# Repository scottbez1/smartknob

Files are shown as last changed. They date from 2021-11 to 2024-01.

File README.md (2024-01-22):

# SmartKnob
SmartKnob is an open-source input device with software-configurable endstops and virtual detents.

A brushless gimbal motor is paired with a magnetic encoder to provide closed-loop torque feedback control, making it
possible to dynamically create and adjust the feel of detents and endstops.

Join the [Discord community](https://discord.gg/5jyhjcbTnR) to discuss the project with others, show off your build, or help answer each others' questions!




# Designs

## SmartKnob View
The "SmartKnob View" is the premium SmartKnob experience with an integrated display shown in my [demo video](https://www.youtube.com/watch?v=ip641WmY4pA). Under active development.

🎉 **Motors are [now available](https://www.sparkfun.com/products/20441)!** If you've been following this project,
you'll know that the recommended motors went out of stock nearly immediately after it was published.
Thanks to [the community](https://github.com/scottbez1/smartknob/issues/16#issuecomment-1094482805%5D), we were able to
identify the likely original manufacturer, and recently SparkFun Electronics has been getting them produced and regularly
[stocking them](https://www.sparkfun.com/products/20441)! (However, they've been selling out quickly each time they restock, so definitely sign up for backorder notifications if they're out of stock when you check). Thanks to everyone who helped search and investigate different
motor options along the way!

Features:
 - 240x240 round LCD ("GC9A01"), protected by 39.5mm watch glass on rotor
 - BLDC gimbal motor, with a hollow shaft for mechanically & electrically connecting the LCD
 - Powered by ESP32-PICO-V3-02 (Lilygo TMicro32 Plus module)
 - PCB flexure and SMD resistors used as strain gauges for press detection (haptic feedback provided via the motor)
 - 8 side-firing RGB LEDs (SK6812-SIDE-A) illuminate ring around the knob
 - USB-C (2.0) connector for 5V power and serial data/programming (CH340)
 - VEML7700 ambient light sensor for automatic backlight & LED intensity adjustment
 - Versatile back plate for mounting - use either 4x screws, or 2x 3M medium Command strips (with cutouts for accessing removal tabs after installation)
 - Front cover snaps on for easy access to the PCB

**Current status:** Not recommended for general use, but may be a fun project for an advanced electronics hobbyist.

### Demo video

<a href="https://www.youtube.com/watch?v=ip641WmY4pA">
    
</a>

### How it works
<a href="https://www.youtube.com/watch?v=Q76dMggUH1M">
    
</a>

### 3D CAD

Exploded view

Latest Fusion 360 Model: https://a360.co/3BzkU0n

#### DEMO: video editor timeline control

If you edit audio/video, imagine having a jog wheel where you could _feel_ the clip boundaries as you scrolled through the timeline. Then switch to playback speed control, with a wheel that's spring-loaded to return to "paused," with snaps at 1x, 2x, 4x, etc. The SmartKnob can do this; it just needs some software integrations to be written. Check out a demo using a SmartKnob prototype to control a mock video timeline:

<a href="https://www.youtube.com/watch?v=J9192DfZplk">
    
</a>

(you can actually try this demo yourself if you've already built a SmartKnob; plug it in over USB and go to https://scottbez1.github.io/smartknob/)

### Build your own?

While this is a "DIY" open-source project, it is not yet a mature plug-and-play project. If you intend to build your own, note that it requires advanced soldering experience to build - very small-pitch surface-mount soldering is required (reflow or hot air recommended), and assembly is quite time-consuming and delicate. Please go into it with the expectation that you will almost certainly need to be able to troubleshoot some hardware and firmware issues yourself - I recommend reviewing/understanding the schematics and basic firmware before jumping in!

More documentation on the BOM and what parts you need to order is coming in the future - thanks so much for your interest! Follow me on [Twitter](https://twitter.com/scottbez1) for the latest updates on this and other projects.

View the latest auto-generated (untested) [Base PCB Interactive BOM](https://smartknob-artifacts.s3.us-west-1.amazonaws.com/master/electronics/view_base-ibom.html) and [Screen PCB Interactive BOM](https://smartknob-artifacts.s3.us-west-1.amazonaws.com/master/electronics/view_screen-ibom.html) (or, the combined [BOM csv](https://smartknob-artifacts.s3.us-west-1.amazonaws.com/master/electronics/view_base-bom.csv)) for electronics/hardware parts list. ⚠️ These are auto-generated from the latest untested revision on GitHub. For tested/stable/recommended artifacts, use a [release](https://github.com/scottbez1/smartknob/releases) instead.

A few miscellaneous notes in the meantime:

 - There's limited space inside the LCD mount for wiring, and 8 wires need to fit through the hole in the center. I used 30 AWG wire-wrapping wire. Enamel-coated wire would probably work too.
 - Older versions of the design (as seen in the videos) used glued-on BF350-3AA strain gauges to detect presses; in v0.5 these were replaced with footprints for SMD resistors, which exhibit similar properties when stretched/compressed and are much easier to assemble. 
 - The TMC6300 is _tiny_ and has a bottom pad, so I would seriously consider getting a stencil along with the PCB order. Even with the stencil I needed to manually clean up some bridging afterward; I _highly_ recommend Chip Quik NC191 gel flux, available on [Amazon](https://amzn.to/3MGDSr5) (or use this [non-affiliate link](https://www.amazon.com/Smooth-Flow-No-Clean-syringe-plunger/dp/B08KJPG3NZ) instead) or from your electronics distributor of choice. Flux is also very helpful when soldering the LCD ribbon cable to to screen PCB.
 - For breadboard prototyping, the [TMC6300-BOB](https://www.trinamic.com/support/eval-kits/details/tmc6300-bob/) or SparkFun's [TMC6300 driver board](https://www.sparkfun.com/products/21867) are awesome and way easier to work with than the bare chip if you just want to play around with low current BLDC motors
 - For AliExpress purchases: I highly recommend **only** using AliExpress Standard Shipping (purchasing in the US). I have had multiple purchases take months or never get delivered when purchased with Cainiao or other low cost shipping options, whereas AliExpress Standard is very reliable and generally faster in my experience.
 - Make sure to check the [open issues](https://github.com/scottbez1/smartknob/issues) - this design is not yet "stable", so beware that everything may not go smoothly.

Future plans:
 - consider switch to using an ESP32-S3-MINI-1 module
 - get wifi configured and working (probably MQTT?). Currently memory is an issue with the full display framebuffer sprite. PSRAM might fix this (requires newer ESP-IDF & unreleased Arduino core, and from a brief test I got horrible performance with PSRAM enabled), or the next item might help reduce memory:
 - migrate to LVGL, for better display rendering and easy support for menus, etc. Shouldn't require a full 240x240x24b framebuffer in memory, freeing some for wifi, etc.
 - Home Assistant integration, or other real-world applications
 - ???
 - [Profit](https://github.com/sponsors/scottbez1/) 😉

#### Already built one?
Check out the [firmware/software documentation](https://paper.dropbox.com/doc/SmartKnob-firmware-and-software--B_oWj~L1dXqHgAqqYmhwwuqzAg-VUb9nq7btuhnHw5KlgJIH)
for tips on getting it programmed and hooking it up to your own software integrations.

If you've already uploaded the standard firmware and gone through the calibration process (see guide linked above if you don't know what this means),
go to https://scottbez1.github.io/smartknob/ to try out an interactive web-based demo that uses Web Serial to talk to a SmartKnob that's plugged into your
computer's USB port!

#### Base PCB

<a href="https://smartknob-artifacts.s3.us-west-1.amazonaws.com/master/electronics/view_base-front-3d.png">
    
</a>
<a href="https://smartknob-artifacts.s3.us-west-1.amazonaws.com/master/electronics/view_base-back-3d.png">
    
</a>

Ordering notes: use white soldermask, for reflecting light from RGB LED ring around the knob. Should be 1.2mm thick (not "standard" 1.6mm).

If you are ordering a stencil for solder paste from JLCPCB and plan to apply paste by hand (as
[shown in the video](https://youtu.be/Q76dMggUH1M?t=372)) without a stencil frame/machine, make sure to select
**"Customized size"** and enter smaller dimensions (e.g. 100mm x 100mm) to avoid getting a much larger stencil than you
need. This will also likely reduce the cost of shipping substantially! Also, select only the **Top** side; the bottom
only has 2 SMT components - the motor connector and VEML7700 ALS - so it's not worth getting a stencil for that.

Latest auto-generated (untested and likely broken!) artifacts⚠️:

[Schematic](https://smartknob-artifacts.s3.us-west-1.amazonaws.com/master/electronics/view_base-schematic.pdf)

[Interactive BOM](https://smartknob-artifacts.s3.us-west-1.amazonaws.com/master/electronics/view_base-ibom.html)

[PCB Packet](https://smartknob-artifacts.s3.us-west-1.amazonaws.com/master/electronics/view_base-pcb-packet.pdf)

[Gerbers](https://smartknob-artifacts.s3.us-west-1.amazonaws.com/master/electronics/view_base-jlc/gerbers.zip)

⚠️ For tested/stable/recommended artifacts, use a [release](https://github.com/scottbez1/smartknob/releases) instead.

#### Screen PCB

<a href="https://smartknob-artifacts.s3.us-west-1.amazonaws.com/master/electronics/view_screen-front-3d.png">
    
</a>
<a href="https://smartknob-artifacts.s3.us-west-1.amazonaws.com/master/electronics/view_screen-back-3d.png">
    
</a>

Ordering notes: Must be 1.2mm thick (not "standard" 1.6mm) per mechanical design. (The PCB silkscreen mentions 0.6mm thickness - this is the thickness of the **VHB tape** for adhering the LCD; the PCB should be 1.2mm thick)

There are few enough components on the Screen PCB that I chose to hand-solder them rather than reflow with solder paste
and a stencil, but if you order a stencil, see the note above about selecting a "Customized size" to be easier to
handle and save on shipping. Also make sure to select the **Bottom** side only; all the components are on the bottom
side of the screen PCB.

Latest auto-generated (untested and likely broken!) artifacts⚠️:

[Schematic](https://smartknob-artifacts.s3.us-west-1.amazonaws.com/master/electronics/view_screen-schematic.pdf)

[Interactive BOM](https://smartknob-artifacts.s3.us-west-1.amazonaws.com/master/electronics/view_screen-ibom.html)

[PCB Packet](https://smartknob-artifacts.s3.us-west-1.amazonaws.com/master/electronics/view_screen-pcb-packet.pdf)

[Gerbers](https://smartknob-artifacts.s3.us-west-1.amazonaws.com/master/electronics/view_screen-jlc/gerbers.zip)

⚠️ For tested/stable/recommended artifacts, use a [release](https://github.com/scottbez1/smartknob/releases) instead.

#### Printed parts
You will need six printed parts. The current stable designs can be found as STL assets in the [v185 mechanical release](https://github.com/scottbez1/smartknob/releases/tag/releases%2Fmechanical%2Fv185-dummy-tag) or you can export the latest untested designs from the CAD model by opening it in Fusion 360: https://a360.co/3BzkU0n

The parts can _probably_ be FDM 3D printed with a well-tuned printer, but the parts shown in videos/photos were MJF printed in nylon for tight tolerances and better surface finish. 

If you wanted a simpler build, you could omit the LCD and just merge the knob + glass from the model into a single STL to get a closed-top knob.

Export and print the following 6 parts:
* `Enclosure`
* `Knob` (RotorAssembly->KnobAssembly->Knob)
* `ScreenPlatform`
* `RotorSpacer` (RotorAssembly->RotorSpacer)
* `MountBase`
* `BackPlate`

⚠️ If you opt to go for MJF Nylon printing from JLCPCB, their system may complain about `< 0.8mm wall thickness detected` on the `MountBase`, `ScreenPlatform` and `RotorSpacer` parts. This appears to be a false positive, possibly on some of the print tapers. You should be able to ignore this, as all print orders at JLCPCB are subject to a final manual review, and they will contact you by email if there are any job-stopping issues or risks with your prints.

## NanoFOC (3rd party)
If you're looking to tinker with FOC/haptic feedback, but don't want to build a full SmartKnob View yourself, I can
recommend the NanoFOC DevKit++, an [open-source design](https://github.com/katbinaris/nanofoc_devkit) made and
[sold](https://store.binaris.io/products/nanofoc-devkit) by a member of the SmartKnob community! It's super compact
and is a great testbed or core for building your own BLDC-based haptic input device.

Image of the NanoFOC PCB

The NanoFOC uses an ESP32-S3, and the SmartKnob firmware works on it out of the box; just select the `nanofoc`
environment in PlatformIO rather than the `view` environment when uploading.

# Frequently Asked Questions (FAQ)

### Can I use this cheap gimbal BLDC motor I found on AliExpress?

I can't stop you, but I will caution that **you probably won't be super happy with it** depending on your intended application.

Nearly every off-the-shelf BLDC gimbal motor that the community has tested (which is pretty much ALL the cheap ones you'll find on AliExpress, trust me) has
_moderate to severge cogging_. That means the motor wants to snap to certain positions by itself even when unpowered. This means you won't be able to get
completely smooth rotation when virtual detents are turned off, and the motor's cogging may interfere with or overpower the virtual detents, particularly if
you set them to lower strength or make then very fine-grained.

The recommended motor is definitely the best (i.e. lowest cogging) off-the-shelf motor we've come across so far, and is the only readily-available motor
that I would consider "good" for this application.

If you've found another motor that is completely smooth when unpowered, we'd LOVE to hear about it in the discord; if you're wondering about some cheap motor
you saw online, either just order one and try it for yourself, or ask about it in discord but don't be surprised (or offended) if the response you get is
something terse like "nope, no good".

### How much does it cost?

I wish I could tell you now, but I don't actually know off the top of my head. Check back soon - I've only built a few so far, which was the result of a bunch of tinkering and prototyping over an extended period, so I don't have all the expenses tallied up yet. Probably less than $200 in parts? But some items have gotten more expensive, and you may be limited by minimum order quantities or shipping charges from multiple separate suppliers.

### Does it work with XYZ?

Not yet, regardless of whatever "XYZ" you're thinking of. So far I've only implemented enough firmware for the demo shown in the video, so you can't actually use it for anything productive yet. The basic detent configuration API is there, but not much else. Lots of firmware work remains to be done. If you build one, I'd love your help adding support for "XYZ" though!

### Can I buy one as a kit or already assembled?

Probably not? Or at least, I don't have any immediate plans to sell them myself. It's not that I don't want you to be happy, but hardware is a hard business and I just work on this stuff in my free time.

It's open source with a fairly permissive license though, so in theory anyone could start offering kits/assemblies. If someone does go down that route of selling them, note that attribution is
 _required_ (and I wouldn't say no to [royalties/tips/thanks](https://github.com/sponsors/scottbez1/) if you're in a giving mood 🙂).

# Firmware and Software
More extensive documentation of the firmware and software (and how to get started) can be found in the dedicated [SmartKnob Firmware and Software Guide](https://paper.dropbox.com/doc/SmartKnob-firmware-and-software--Byho6npe9XvZLZLxJ_8bK5TqAg-VUb9nq7btuhnHw5KlgJIH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)

## General Component Info

### Magnetic encoders

#### MT6701 (MagnTek)
Excellent sensor at a reasonable price - highly recommended. Less noisy than TLV493D, and more responsive (control loop is more stable) using SSI.

 - Lots of IO options - SSI, I2C, and ABZ - should offer good response latency
 - SSI includes CRC to validate data
 - No power-down or low-power options - may not be ideal for battery-powered devices
 - Not available from US distributors (Mouser, Digi-Key)

[Datasheet](http://www.magntek.com.cn/upload/MT6701_Rev.1.5.pdf)

[Ordering (LCSC)](https://lcsc.com/product-detail/Angle-Linear-Position-Sensors_Magn-Tek-MT6701CT-STD_C2856764.html)

#### TLV493D (Infineon)
Not used in the SmartKnob view, but a common/popular magnetic encoder in general. It's a mediocre choice for a haptic feedback implementation. Easy to prototype with using [Adafruit's QWIIC breakout board](https://www.adafruit.com/product/4366).

In my testing, it's noisy, requiring filtering/smoothing that can slow responsiveness, hurting control loop stability. Or, with less filtering, the noise
can easily be "amplified" by the derivative component in the PID motor torque controller, causing audible (and tactile) humming/buzzing.

But the bigger issue is that there is apparently a known silicon issue that causes the internal ADC to sometimes completely lock up, requiring a full reset and re-configuration, which can cause delays/gaps in data! See section
5.6 in the [User Manual](https://www.infineon.com/dgdl/Infineon-TLV493D-A1B6_3DMagnetic-UM-v01_03-EN.pdf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)

    In the Master Controlled Mode (MCM) or the Fast Mode (FM) the ADC conversion may hang up. A hang up can
    be detected by:
     - Frame Counter (FRM) counter stucks and does not increment anymore.

In my experience testing 4 different Adafruit breakout boards, 2 of them (50%) regularly exhibit this lockup behavior within a minute or two of use. It is possible to detect and auto-reset (and there is code in the project to do so), but it is slow and may cause undesirable jumps/delays if the sensor locks up often.

[Datasheet](https://www.mouser.com/datasheet/2/196/Infineon_TLV493D_A1B6_DataSheet_v01_10_EN-1227967.pdf)

#### AS5600 (AMS)
A mediocre choice. Cheap breakout boards are readily available.

In my testing, it's fairly noisy (anecdotally, noisier than the TLV493d), requiring filtering/smoothing that can slow responsiveness, hurting control loop stability. Additionally, it saturates at a lower magnetic field strength than other sensors I tested, requiring a significant air gap (8-10mm) when used with a strong neodymium diametric magnet like [Radial Magnets 8995](https://www.digikey.com/en/products/detail/radial-magnets-inc/8995/5126077).

[Datasheet](https://ams.com/documents/20143/36005/AS5600_DS000365_5-00.pdf)

### Motor drivers
#### TMC6300-LA
This is a relatively new IC and it's a perfect match! There generally aren't any other drivers (with integrated fets) that meet the requirements for the low-voltage and low-current motors used in this project (DRV8316 might work, but has not been tested).

Highlights:
 - 2-11V DC motor supply input
 - Up to 1.2A RMS
 - Tiny (3x3mm QFN)

 [Datasheet](https://www.trinamic.com/fileadmin/assets/Products/ICs_Documents/TMC6300_datasheet_rev1.07.pdf)

 [Product page](https://www.trinamic.com/products/integrated-circuits/details/tmc6300-la/)

### Motors
#### 32mm Rotor, Hollow Shaft, Diametric magnet
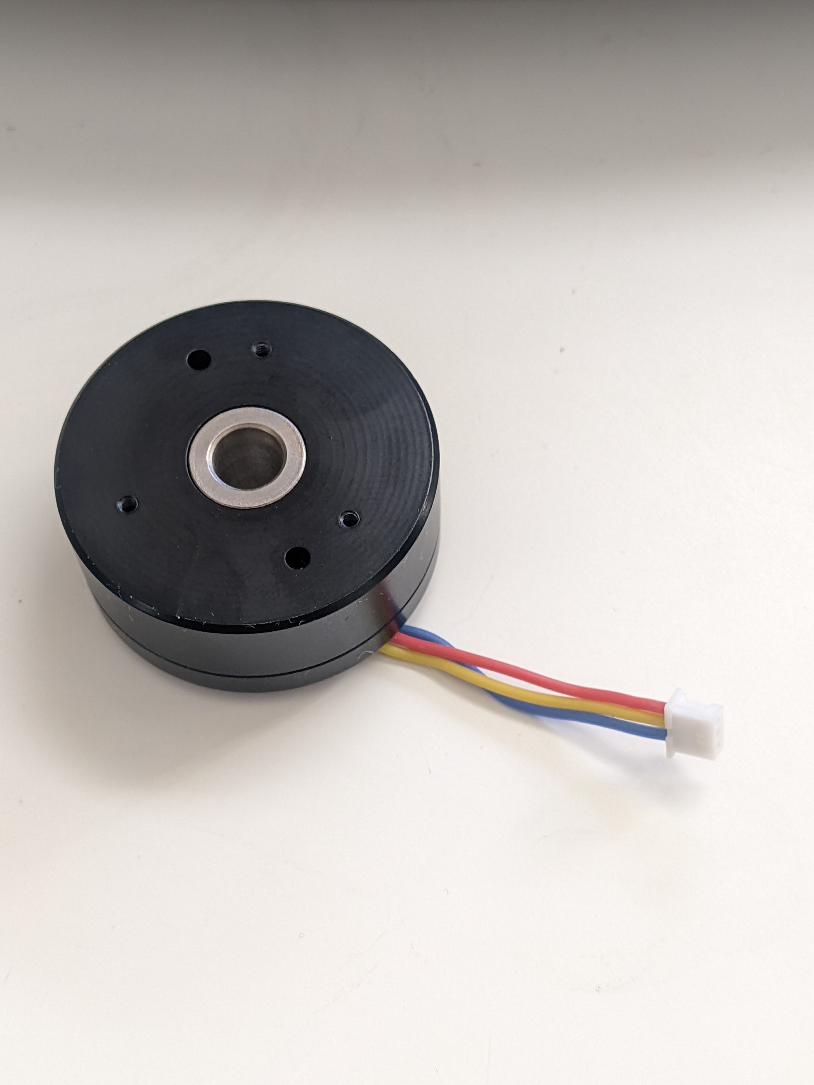
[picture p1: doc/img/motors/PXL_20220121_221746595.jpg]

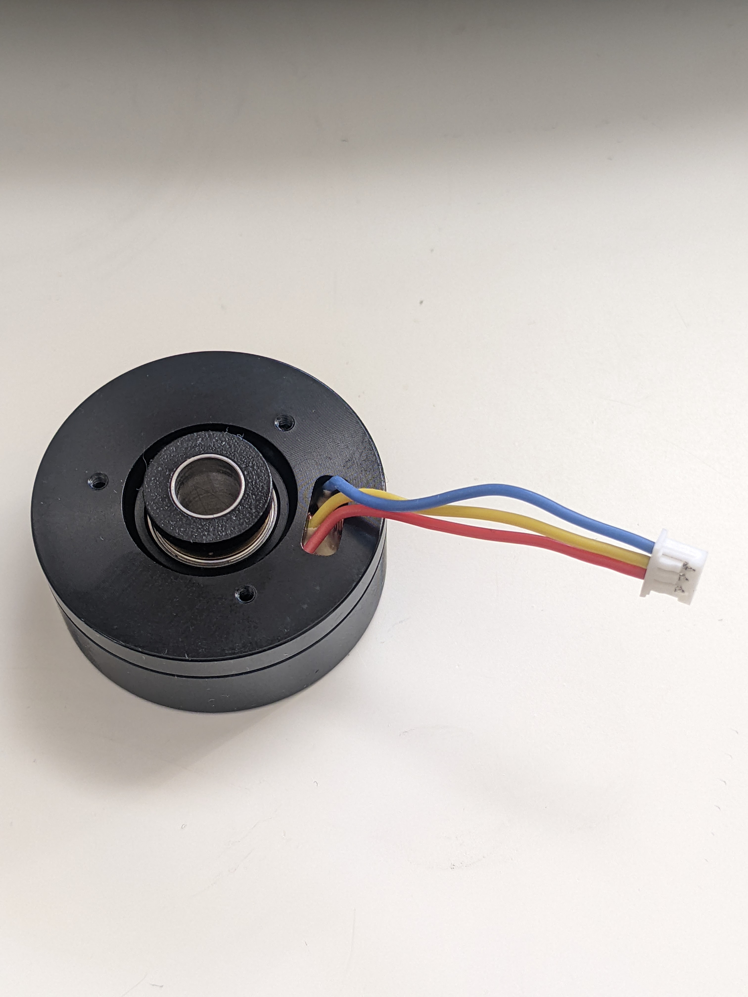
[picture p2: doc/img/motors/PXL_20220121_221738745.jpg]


- 32mm rotor
- 15mm overall height (including magnet), 12.75mm height w/o magnet, 9mm rotor height
- low/zero cogging - excellent for completely smooth input
- 5.9mm hollow shaft
- built-in diametric magnet for encoder
- Proven option

This is overall the easiest motor to get started with. Low cogging and a built-in diametric magnet are great!

Available [from SparkFun](https://www.sparkfun.com/products/20441)!

# Acknowledgements
This project was greatly inspired by Jesse Schoch's video "[haptic textures and virtual detents](https://www.youtube.com/watch?v=1gPQfDkX3BU)" and the
corresponding [discussion in the SimpleFOC community](https://community.simplefoc.com/t/haptic-textures/301). Seriously, this project wouldn't exist if not for that video - thank you Jesse!

# License

This project is licensed under Apache v2 (software, electronics, documentation) and Creative Commons Attribution 4.0 (hardware/mechanical) (see [LICENSE.txt](LICENSE.txt) and [Creative Commons](https://creativecommons.org/licenses/by/4.0/)).

    Copyright 2022 Scott Bezek
    
    Licensed under the Apache License, Version 2.0 (the "License");
    you may not use this file except in compliance with the License.
    You may obtain a copy of the License at
    
        http://www.apache.org/licenses/LICENSE-2.0
    
    Unless required by applicable law or agreed to in writing, software
    distributed under the License is distributed on an "AS IS" BASIS,
    WITHOUT WARRANTIES OR CONDITIONS OF ANY KIND, either express or implied.
    See the License for the specific language governing permissions and
    limitations under the License.

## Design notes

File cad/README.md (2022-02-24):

# CAD

Most CAD work is done in Fusion 360 and versioned outside of this git repo.

# Assemblies
## SmartKnob View
 - [Complete SmartKnob View assembly](https://a360.co/3BzkU0n)

## Handheld
 - [Case bottom](https://a360.co/3LM82se) For breadboard with power rails removed.
 - [Motor adapter](https://a360.co/3LO03eC) Connects motor to Adafruit TLV493d adapter board, and screws into Case
 - [Thumbwheel](https://a360.co/3H3jSee) Test thumbwheel for motor rotor, for turning from the side

# Motors
Note that all measurements were done by hand and will be approximate. Chamfers & fillets are approximated.

## 32mm
 - [Motor model](https://a360.co/3H8LUFi)

## 17mm
 - [Motor model](https://a360.co/3sYa93Y)
 - [Spacer](https://a360.co/3H3xh5M) (screw at the bottom is replaced with a longer M1.4 screw with this spacer inserted; diametric magnet is glued to screw)
 - [Dummy test jig](https://a360.co/3sPQgvB)

 ## 15mm
 - [Motor model](https://a360.co/34N1nOa)
 - [Magnet spacer](https://a360.co/3532Tvb)
 - [Magnet gluing jig](https://a360.co/3I1xbx6)
 - [Adapter](https://a360.co/35gC86B) - mount motor to Adafruit TLV493d adapter board

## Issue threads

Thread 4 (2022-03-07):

Increase vertical clearance between LCD and knob

scottbez1, 2022-03-07:
Could use another ~0.5mm between LCD and the inside/inner-bottom face of the knob, to account for assembly imperfections, to ensure the knob doesn't scrape on the screen.

It should be ok to decrease the vertical clearance below the screen pcb correspondingly; there's more clearance here than necessary.

scottbez1, 2022-03-14:
Increased by 0.5mm in v175 & v181

Closed 2022-03-14.

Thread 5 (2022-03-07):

Consider increasing diameter of screen PCB

scottbez1, 2022-03-07:
To avoid LED light leakage around the LCD, it might make sense to increase the PCB's diameter. Might also be helpful to add silkscreen alignment marks on the top side to help with centering the LCD.

Need to make sure it's still narrow enough for the knob/rotor to slide past it during assembly.

scottbez1, 2022-03-14:
Decided to add a light baffle to the MountBase instead, in v179. The light baffle is right above the LEDs so should be more effective at blocking light (any remaining light leakage will have a higher incident angle with ID wall of the knob compared to using the screen PCB as a baffle). It will require supports for FDM printing, but this shouldn't be a big deal since this is non-cosmetic and tolerances are not an issue on the underside of the light baffle (plenty of space between the baffle and LED for vestigial support blemishes)

Keeping screen pcb diameter <= lcd diameter is preferable to avoid having exposed VHB when viewed from the top (or else you'd need to trim the VHB inset from the PCB edge...)

Closed 2022-03-14.

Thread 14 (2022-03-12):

Idea: ethernet/PoE

nagyrobi, 2022-03-12:
Is there any plan to have a version supporting wired Ethernet connetion?

ESP32 can accomodate with various Ethernet PHY chips, also combined with an 802.3af PoE supply this project could really kick ass in the home automation world. Think of this also as mounted on wall on the end of a CAT5 cable supplying both data and power...

scottbez1, 2022-03-13:
No plans for Ethernet. It would definitely be cool, but probably not something I will personally prioritize at the moment. My main priorities are:
- better documentation
- firmware improvements (graphics, configuration api, serial protocol, getting wifi working)

But the other issue that comes up is limited IO - with the current ESP32 module I'm using, all outputs are currently in use (except IO0 I guess) and the only open pins are inputs (34, 35, and 39).

The LCD (6 GPIO) and motor driver (7 GPIO) are both IO heavy, and then there's I2C, magnetic sensor, and strain gauge amplifier, so it would require a pretty substantial change to be able to free up pins to support an ethernet PHY.

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

There's probably a hybrid approach where you use an external ethernet<->serial adapter and connect this in place of the CH340 USB serial interface, but I'm not familiar with what's available in that space, or how to integrate it. In that case it would be helpful to expose RX and TX as testpoints for easier connection.

nagyrobi, 2022-03-14:
I suggest for develompent on the longer term... maybe you could use a GPIO expander like MCP23017 for more basic stuff...

Ethernet-Serial conversion limits functionality a lot, as there's an extra middleware needed to convert serial-like protocol to whatever is needed. Ethernet connection should be equivalent to wifi in terms of functionality.

scottbez1, 2022-03-15:
Added RX/TX testpoints, so hardwired serial communication without a USB connection is easier to hook up if desired.

However, the remainder of the discussion in this issue regarding first-class ethernet support is outside the scope of planned features, so in the interest of keeping the issues list clean, closing this as wontfix.

scottbez1, 2022-04-07:
Per #51, I'm reopening this issue as a general place for brainstorming/discussion around ethernet and PoE. Like I mentioned in that issue, I want to keep this project extremely focused for now, so I don't see ethernet support realistically being added any time soon, but doesn't hurt to have a place (this thread) for discussion in the meantime

austinscreations, 2022-04-13:
for POE i've been using https://www.aliexpress.com/item/1005002768318128.html
(keyword: SDAPO DP1435 - should link die)

combined with the w5500 spi ethernet IC - which requires 5 pins. sck, miso, mosi, cs, and a reset pin (not mcu reset - needs to be controllable IO)

Timvrakas, 2022-09-15:
I'm not sure Ethernet is needed for this simple of a device, PoE adds a significant cost and complexity electrically. If you were integrating this into an industrial/home automation system I can see the appeal, but if I were running more than one or two units I think I would quickly prefer RS485 or CAN or BASE-T1L or similar to link them to a controller that in turn had Ethernet.

If you're looking for a PoE module, I will recommend https://silvertel.com/ they make high quality PoE modules.

sanderkooger, 2023-10-19:
Another option would maybe be skip the POE and Ethernet connectivity, Mount the smart knob on a (in wall) switch box and use the power thats already there? Then use WIFI for communication.

Is this a viable option too?

sanderkooger, 2023-10-19:
@scottbez1 Congrats on this project BTW, This could be the start of something really cool.

At the moment, I'm researching lights control for my home. If Wi-Fi becomes available and i could have the knob send out API requests over Wi-Fi. I should be golden. I'm also looking into thermostats that i can talk too over an API.

Have you ever thought of promoting your project on the Wled https://github.com/Aircoookie/WLED

I think you would find a lot more enthusiasts there who have and electronic knowledge and could maybe contribute.

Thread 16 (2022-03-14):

Motor out of stock

mattkerrison, 2022-03-14:
Not a major issue as you've said you've got several others on the way for testing, but the link to the motor you used is now out of stock:

[AliExpress](https://www.aliexpress.com/item/1005001384349991.html)

scottbez1, 2022-03-14:
Yeah, I'm hoping this is just a temporary out of stock issue, but the seller actually has another listing that looks essentially identical (though a tiny bit more expensive) and is still in stock (for now) - https://www.aliexpress.com/item/4001356858801.html

I've ordered a handful of those myself and will confirm whether they're the same in ~2 weeks when they arrive :stuck_out_tongue: Probably worth snagging a few now regardless since they're pretty cheap.

My fear is that they may just be selling off "new old stock" from some short-lived product and the motors are not actively being manufactured any longer, in which case the interest in this project could quickly consume what's available. :crossed_fingers: Hopefully that's not the case though, as there are basically zero other cheap options for hollow shaft BLDC motors with low KV and zero cogging torque that I could find...

SpuriousGer, 2022-03-25:
Your update on March 24th seems quite discouraging, does this mean the project is dead? Seems like one of the coolest ones I've seen in ages.

C44Supra, 2022-03-25:
It gets worse, the other listing that @scottbez1 linked to is gone now too. I had an order for a couple of those and that order was simply cancelled earlier this morning, so that double listing seems to have been an oversight. The motors from that seller (and two other sellers as well) that looked similar by had wires running through the hollow shaft already, those have also been removed. Well not removed, I created two orders from separate sellers last night and both of those items have been changed into a completely different item. I haven't been able to find a replacement motor yet.

I'm not sure what other motors @scottbez1 has bought to test, but I would love to know. It would be very helpful to know which motors we should avoid specifically.

scottbez1, 2022-03-25:
Responding from my phone, so pardon the brevity.

I don't want to call the project dead quite so soon, but it's certainly not
looking very good at all...

Regarding other motors, I basically ordered every single small BLDC from
that AliExpress seller (which is most of the cheap motors I could find on
AliExpress in general) and there's not good news there, unfortunately. All
of the other hollow-shaft motors had noticeable or substantial cogging,
making them poor candidates.

I'll follow up with more details when I have some time this weekend,
including a list of all the motors I've personally checked.

C44Supra, 2022-03-25:
I certainly wouldn't call it dead in the water, just needs some adjustments for a more widely available motor. I'm tempted to grab a more common 2804 or maybe 2204. Lots of varieties though and not a whole lot that either have an axial magnet or room for one.

SpuriousGer, 2022-03-25:
> Responding from my phone, so pardon the brevity. I don't want to call the project dead quite so soon, but it's certainly not looking very good at all... Regarding other motors, I basically ordered every single small BLDC from that AliExpress seller (which is most of the cheap motors I could find on AliExpress in general) and there's not good news there, unfortunately. All of the other hollow-shaft motors had noticeable or substantial cogging, making them poor candidates. I'll follow up with more details when I have some time this weekend, including a list of all the motors I've personally checked.

You mention cheap, is it a prerequisite that it is really cheap or are there other motors that might fit the bill but are more expensive?

C44Supra, 2022-03-25:
@scottbez1 would be helpful to know what sort of BLDC motor you're using at the moment. From what I understand the majority of cogging is a result of the type and size of magnets used in the rotating part. In an effort to generate as much torque as possible, most manufacturers opt for neodymium magnets which are significantly more powerful compared to ferrite magnets.

jimius, 2022-03-26:
I don't know a lot about motors, but I did find this:
https://store.cubemars.com/ from a company called Tmotors (
https://uav-en.tmotor.com/).
Again, no idea if the specs match anything you need.

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

dsamarin1, 2022-03-26:
Seconding what @C44Supra said, perhaps logging here the specs of your currently best-performing motor so the group can help hunt down a replacement, especially once the AliExpress pages disappear. I'm thinking these are important: Critical dimensions, Kv, electrical specs (ex. maybe max torque can indicate something else useful), keywords. Others?

In the future, the move is probably a redesign for the more common outrunner motors on hobby RC websites. Considering tackling part of this myself.

LeonBentrup, 2022-03-27:
It looks like [newegg](https://www.newegg.com/p/298-00HJ-001V2) has the motor but only with a slipring installed. removing that wouldnt be a problem, but the 50$ pricetag is. i think the best way going forward would be using a standard gimbal motor and putting on a diametrical ringmagnet from [mcmastercarr](https://www.mcmaster.com/ring-magnets/direction-of-magnetization~through-diameter/) or so. something like those 2804, 2805or 3413 look more common and could propably be used

C44Supra, 2022-03-27:
@LeonBentrup that listing on Newegg is from a chinese reseller as well. It was listed by at least 3 different vendors on AliExpress but all three have removed the exact same listings at the same time. I'd say there's good chance it's one and the same vendor, just active under a couple of different names. That said, I did get a reply from the AliExpress seller earlier today:

> Sorry to tell you that we can't send this item out. A local buyer picked all this item a few days ago and our workmate forget to remind us to end this listing.
We contacted several suppliers and they don't have this item in stock. And also can't give sure reply when the item will be available.
But we have the other similar item in our shop,could you please check it meet your need or not?

The other item they are referring to is https://www.aliexpress.com/item/1005003751799249.html It looks somewhat similar but is missing the diametrical magnet. There's also not enough shaft protruding to stick a magnet onto so that would be a no good either.

It's also quite problematic that their motor numbers seem to reference the outer diameter and height of the entire motor, where as other suppliers generally reference the internal dimensions of the actual motor parts. The 3413 for instance is pretty much the same as a 2804.

I did "some" looking around on AliBaba last night / this morning ( / what day is it again?), and found a supplier that has a motor that shows potential. They're not too expensive, have a 7mm diameter protruding shaft on the bottom and looks to be good design. I've contacted them and are waiting for a reply with more data about that specific motor.

A quick search on Amazon led me to some 10x3x7 (outer diameter x thickness x inner diameter) diametric magnets. I think thinner ones would work, too, though.

LeonBentrup, 2022-03-27:
@C44Supra Does it have to to be a motor with a stick out shaft? for example the mks servo42 just uses superglue and two of those are running fine on my 3d printer. its not a hollow shaft there but those [cheap 2804](https://de.aliexpress.com/item/1005001968864724.html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,scm-url:1007.40000.267768.0,pvid:cdc11d7c-d8bd-49ea-8f4c-22b666c9050f,tpp_buckets:668%232846%238112%23502&pdp_ext_f=%257B%2522sku_id%2522%253A%252212000018267338478%2522%252C%2522sceneId%2522%253A%252230050%2522%257D&pdp_pi=-1%253B3.03%253B-1%253B-1%2540salePrice%253BEUR%253Brecommend-recommend) look like you could glue it on there directly. Sticking a 6mm rod with some paper(to not glue the rod in there) down the hollow shaft you could even get it centered pretty good. and since its not turning with 2000 rpm i wouldnt be afraid of the glue giving up
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
jtsfour, 2022-04-01:
@C44Supra

Thanks for the input.  I was just now doing some digging into the magnets.  What if we standardized around a motor design even with neodymium magnets (Like the 2804).  Couldn't we just remove the Neodymium magnets from the rotor and replace it with a Ferrite Ring of our own specifications?  How are these magnets installed?  Could we use a heat gun and pull them?

I found this magnet supplier that does custom multipolar ferrite rings.  Maybe this could be an easier option over finding motors that have been specifically built weaker and cheaper.  We could use a small crowdsource and buy a couple thousand and use them collectively.

https://www.hsmagnets.com/product/customized-radial-multipole-ferrite-rotor-magnets/

I am not an engineer.  Maybe someone with more experience could weigh in on this thought?

C44Supra, 2022-04-01:
@jtsfour

That would certainly be an option. I don't have any motors on hand just yet, but I suspect the magnets are being glued in, likely with a two part epoxy of sorts. The likelyhood of removing the magnets without destroying them or the rotor itself are likely slim to none.

That said, you may be on to something. I'll ask the manufacturers if they'd be willing to sell motors without magnets in the rotor at all.

Multipolar ring magnets can be found in all shapes and sizes on Alibaba as well. Finding one that fits the bill might be a bit of a challenge though.

mcmadhatter, 2022-04-01:
I have a "Power Motor GBM2804R 2804 Gimbal Motor with Aluminum case /Slipring /AS5048A Magnetic Encoder for camera stabilizer" on order for something else, but I'll try it out and see what it is like beforehand.

scottbez1, 2022-04-01:
Just for the heck of it, I submitted an Alibaba RFQ with the details and photos of the existing motors (32mm rotor, 6mm ID, 14P12N, etc), just in case the original manufacturer is still around and can easily spin up production of it again, or in case another manufacturer is able to produce an identical product. Certainly would be nice if it can be found and avoid the need to redesign the mechanics. Probably unlikely, but figured it's worth a shot.

scottbez1, 2022-04-02:
I've ordered some samples of the 2608 with ring magnet (from "Flash Hobby" Huizhou Feishun Technology), asking for a couple 5 ohm and a couple with 8 ohm windings to see how they compare.

Apparently there weren't readily available ferrite ring magnets for the 2606 size, so they will not make samples of that size for now.

Samples will ship via DHL Express, so depending on how long manufacturing takes I would hope to have them within a few weeks to evaluate them.

A big thank you to all the GitHub [sponsors](https://github.com/sponsors/scottbez1/) for helping fund experimentation like this! :heart:

If you're interested in eventually purchasing a motor (still a long way away and motor still TBD) - can you fill out [this quick anonymous survey](https://forms.gle/PtuVDrpcA2niVDCL9) so I can get a sense of total interest quantity, geographical distribution, and pricing? To somewhat set expectations, based on what I'm seeing I would guess that it will cost somewhere between US$25-50 per motor unless we can find something suitable that's already being widely manufactured and distributed, unfortunately...

 And of course let me know if you find other interesting motors or suppliers and I am happy to place more sample orders!

scottbez1, 2022-04-02:
@jtsfour thanks for
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

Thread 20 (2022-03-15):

Screen PCB thickness

Zomhad, 2022-03-15:
First of all thanks for open-sourcing this awesome design! I just noticed that the readme states the screen PCB must be 1.2mm thick ("Ordering notes: Must be 1.2mm thick (not "standard" 1.6mm) per mechanical design.") but on the silkscreen of the PCB there's a big "0.6mm thick" label. Probably just a small copy and paste mistake from the ordering notes of the base PCB, thought I'd mention it anyway.

PS: Can't wait for my PCB and parts to arrive and build one up. :-)

scottbez1, 2022-03-15:
Thanks for bringing this up!

Both are actually correct, if you can believe it. 1.2mm thickness PCB is correct, and the 0.6mm thick label on the silkscreen is meant to go with the "VHB 5925" text to clarify that the expectation is for 0.6mm VHB tape as opposed to the more common VHB 5952 (isn't that confusing product numbering?!) which is 1.1mm thick.

Let me think about how to make this more clear though, as I can totally understand the mixup.

I've been thinking about adding virtual footprints to the screen PCB for the double-sided tape, in which case the silkscreen clarification is probably not needed anymore since I can put a part number and clarifying comment for the VHB items which will appear in the auto-generated BOM directly.

scottbez1, 2022-03-15:
(another possible option I'm considering is just switching to 1.1mm VHB 5952 since it's more commonly found anyway, and just add another .5mm of vertical clearance inside the knob to accommodate)

Closed 2022-03-28.

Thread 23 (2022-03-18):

Pick & Place File

tallAldi, 2022-03-18:
Would it be possible to include a simple pick & place file in addition to the bom?
I'm not that experienced with smd soldering and would like to order the pcbs already assembled at factory, at least for the general stuff like resistors and capacitors.

scottbez1, 2022-03-18:
Are you thinking JLCPCB or another manufacturer? In theory this shouldn't be too difficult to support since I'm already using KiKit to export the gerbers (I may have to swap some LCSC part numbers for ones in JLC's PCBA part library), but one potential concern is that the finest pitch/most difficult part, the TMC6300, is not in JLC's part library for assembly so you'd still need to solder it yourself. At that point I'm not sure how much it helps to have the resistors and capacitors pre-assembled...

Here's a photo for reference - the small capacitors here are 0603 and the bigger capacitor is 0805:
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

tallAldi, 2022-03-25:
Yes exactly I was thinking JLCPCB. I think I can adjust the part numbers myself, the important thing to have is the coordinates in the picker files.
If I want to use a different manufacturer I have to adjust the part numbers anyways.
Good point regarding the TMC6300 though, maybe I have to solder that one myself, but then at least I don't have to worry about the rest.

KartoffelToby, 2022-03-30:
maybe pcbway is an option with a https://www.pcbway.com/project/sponsor/ sounds good, looks like its possible to make a "include all" package here with 3D Print and PCB assembled

tallAldi, 2022-04-08:
thanks for the BOM and CPL but I think there is something wrong with your export scripts as the CSVs are not formatted correctly:
`<Error>
<Code>AccessDenied</Code>
<Message>Access Denied</Message>
<RequestId>04005S033CFPDBGC</RequestId>
<HostId>
hrsQX0Zd4Dm7yARZxQnLXX2OTdabTdvb/b2LqfneL4g2Y6e8PpY6g72ds2pVmiQwefNG6p+Uq7I=
</HostId>
</Error>`

D-Buckingham, 2022-06-14:
Dear Scottbez1,
I really enjoy your design and the implementation you did is simply awesome.
I am at the same point as tallAldi and I would really appreciate it, if you could add centroid files in the releases. I tried to extract it myself with altrium from the gerbers, but somewhere I am stuck between errors or incomplete lists...
Thanks a lot!!!
PS: I get the same error message as tallAldi.
PPS: My chosen manufacturer is PCBWay ;)

SpuriousGer, 2022-10-07:
So, I contacted PCBWay and they said they'd be able to support this. What I don't really understand is: what do I need beyond it. I need to upload something here: https://www.pcbway.com/quotesmt.aspx
But what do I fill out and which files do I need to upload?

kquinsland, 2022-10-08:
> What I don't really understand is: what do I need beyond it. I need to upload something here: https://www.pcbway.com/quotesmt.aspx
> But what do I fill out and which files do I need to upload?

They're looking for several files but at a high level, the data they need fits into one of three big groups:

- the grbl files; one for each layer of the PCB. All/Most of these layers should share a common origin or fiducial point and some layers may contain notes about a particular feature or intention. This is typically sent as a ZIP file and it's the bare minimum you need to get a PCB made.
- the list of part numbers. If you're not going to use pcbway parts, there's some additional glue around which parts you supply and which they do. I don't know what this glue looks like, but i'd bet $ that it involves some back/forth with their support staff.
- a file that indicates the X/Y location (relative to the common fiducial / origin) for each of the part number(s).

The third group is commonly called the "pick and place" file... which is being discussed here :D.

The exact format for each will depend on the place doing the work; they all have their own rules around what they can/can't do ... etc.

Google will help you locate the rules / supported features for a board shop and then the rest is figuring out how to get the design software to spit out the files in the format(s) that the board house will accept.

**right now** one of the bigger questions is around _where_ to get the boards made. Not every board shop has the right part(s) in stock. Ideally, there would be a single part supplier that has a close relationship with the board shop so we only needed one set of part numbers.

SpuriousGer, 2022-10-08:
> **right now** one of the bigger questions is around _where_ to get the boards made. Not every board shop has the right part(s) in stock. Ideally, there would be a single part supplier that has a close relationship with the board shop so we only needed one set of part numbers.

Thanks a lot for the thorough reply, very helpful!
I think we have a list of those pick and place files, don't we:
https://smartknob-artifacts.s3.us-west-1.amazonaws.com/master/electronics/view_base-ibom.html
https://smartknob-artifacts.s3.us-west-1.amazonaws.com/master/electronics/view_screen-ibom.html

Or is this again something else?

I am trying to work with PCBWay on how to get this done. But I am so limited in my skills, I basically have two things: money (so I am happy to pay anyone for their time to assemble those lists) and the willingness to engage with them to have prototypes build and take the risk.

kquinsland, 2022-10-08:
> Or is this again something else?

That's a "human friendly" version of the data.  Look at the `LCSC` column on either and compare with the `Mouser` and `Digikey`. No one supplier has a part number for everything that's required which is the biggest blocker at the moment.

> I am trying to work with PCBWay on how to get this done.

See if you can find out what quantity they need for external parts.  I would imagine that it's probably a reasonably big number but if not, then you might be able to coordinate a small group buy.  E.G.: if they're willing to do a production run of only 10 boards using (some) customer supplied / 3rd party parts then you only need to find 10 boards worth of parts from which ever supplier has the parts that PCBWay does not have and ship them to PCBWay.

SpuriousGer, 2022-10-13:
I have received feedback from PCBWay. Attached is the Excel. I would require some help on this. Who could help? I think it looks promising overall.
[T-B2W570125A-5sets-view_base-bom(2022-10-13).xls](https://github.com/scottbez1/smartknob/files/9776060/T-B2W570125A-5sets-view_base-bom.2022-10-13.xls)

SpuriousGer, 2022-11-01:
I hit the next road bump (I guess to be expected as a complete novice), PCBWay is asking for the pick&place(centroid) file for the base PCB. Anyone any clue?

AminKAli, 2023-05-25:
I'd be interested in the group by if that was still happening. @SpuriousGer Let me know if I can help with anything

SpuriousGer, 2023-05-26:
I did order some PCBs from PCBWay and have all the parts, but I never got around to assembling it.
I'd still be interested in the group, I'd be happy to provide funding, but I would need someone to help with instructing PCB and assembling all the required parts.

percramer, 2023-08-08:
I am also interested and I work with pcbway often (also for cnc machining etc). Where did you get stuck with the board Assembly with them? The pick & place location file?

jantyikt, 2023-08-08:
After a few emails, everything was sorted. They used/found a bit of different parts here and there, the ones they had available (+ they couldn't get the heatsink and the tube, which is not a problem anyway). Their first letter was a bit misunderstood, I think, but then it all went about smoothly. The end product looks really good but I did not have time to try out.

sebastienvermeille, 2024-03-04:
Hi guys, did you manage to collect all the required files ? I would like to order also a presoldered pcb as SMD is too difficult for me to solder.

Thank you :)

varunkotian, 2024-09-26:
you can find it here. But these are unverified.

[bom.csv](https://smartknob-artifacts.s3.us-west-1.amazonaws.com/dev/assemblyFiles/electronics/view_base-jlc/bom.csv)
[pos.csv](https://smartknob-artifacts.s3.us-west-1.amazonaws.com/dev/assemblyFiles/electronics/view_base-jlc/pos.csv)

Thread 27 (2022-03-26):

32 mm BLDC Motor isn't for sale anymore :(

18Markus1984, 2022-03-26:
Hello, I saw your video yesterday for the first time and was blown away. I always wanted such a thing, but DIY and not like the Nest thing. I directly made a shopping list for all parts and had no problem to find all the parts besides the BLDC Motor. And also the price for all parts with shipping to Germany is around €85, pretty good. And if the shipping cost for the PCBs weren't that high, it would be even cheaper.

Likewise, I first used the link to find the motor isn't for sale anymore. So I thought maybe find it somewhere else on the internet, but... google pictures said No. I really tried to find the thing with all the product pictures the names of the specifications, but I didn't find it. The only seller for the motor in my opinion was AliExpress. I couldn't find another platform where you could buy this exact motor.

The only motor of similar size I could spot was a bit bigger [one](https://de.aliexpress.com/item/1005003751799249.html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,scm-url:1007.13339.274681.0,pvid:df4ad597-8a5a-450c-8475-9387ba4b90fc,tpp_buckets:668%232846%238111%231996&pdp_ext_f=%257B%2522sku_id%2522%253A%252212000027041443598%2522%252C%2522sceneId%2522%253A%25223339%2522%257D&pdp_pi=-1%253B3.07%253B-1%253B-1%2540salePrice%253BEUR%253Brecommend-recommend)

I could use the [smaller](https://de.aliexpress.com/item/1005003240145615.html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) motor, but you said on your other branch "moderate cogging - not ideal for completely smooth input". I ordered this one, but do you think it is relatively easy to remodel the design for the 34 mm Version? Or is there definitely not enough space, so I had to remodel the complete exterior covering?
Maybe you found a better motor till now.

Happy to hear from you 👍

ioma8, 2022-03-27:
I am also interested where to get such motor.

PaulGoldschmidt, 2022-03-28:
Hey @18Markus1984, I'm also quite interested in building such a knob - additionally, I'm living in Germany (Heidelberg).
If you are interessted in a collaboration, please let me know.

Kind regards,
Paul

C44Supra, 2022-03-28:
@18Markus1984 There's a ticket for the motor stocking issue already: https://github.com/scottbez1/smartknob/issues/16
PCBs shouldn't be that expensive, you can get them made for a couple of dollars and shipped for a few more dollars at JLC. All depends on how patient you are.

18Markus1984, 2022-03-28:
> @18Markus1984 There's a ticket for the motor stocking issue already: #16 PCBs shouldn't be that expensive, you can get them made for a couple of dollars and shipped for a few more dollars at JLC. All depends on how patient you are.

Yes I always order at JLC but if you look at the recent [shipping prices](https://photos.app.goo.gl/VT93cuQ5iBZmSmxy6). You can see that they got a little bit higher. Lowest 16$

18Markus1984, 2022-03-28:
> Hey @18Markus1984, I'm also quite interested in building such a knob - additionally, I'm living in Germany (Heidelberg). If you are interessted in a collaboration, please let me know.
>
> Kind regards, Paul

Ja wäre nice. Schreib mich einfach mal an.

C44Supra, 2022-03-28:
@18Markus1984 @PaulGoldschmidt I'm also in Germany. My PCBs were delivered earlier today. Most of the components I have on hand as well. Just waiting for the AliExpress parts. Problem is that with a different motor there might be some mounting issues.

18Markus1984, 2022-03-28:
> @18Markus1984 @PaulGoldschmidt I'm also in Germany. My PCBs were delivered earlier today. Most of the components I have on hand as well. Just waiting for the AliExpress parts. Problem is that with a different motor there might be some mounting issues.

So you have a spare one? That I don't have to order them?

C44Supra, 2022-03-28:
I have a spare set of PCBs yes. I should have spare components too. I can put the components on for you as well. Probably a good idea with the TMC6300. If you want to put the rest on yourself, I'll leave that up to you.

Horia73, 2022-03-28:
I am also interested in building this knob. If it s someone here that have multiple pcbs and spare parts and wants to sell them please let me know. I m from Romania.

zablotzky, 2022-03-28:
> I have a spare set of PCBs yes. I should have spare components too. I can put the components on for you as well. Probably a good idea with the TMC6300. If you want to put the rest on yourself, I'll leave that up to you.

Oh I would be happy to get one with the components as well! How can we get in touch to get this organised?

Horia73, 2022-03-28:
> > I have a spare set of PCBs yes. I should have spare components too. I can put the components on for you as well. Probably a good idea with the TMC6300. If you want to put the rest on yourself, I'll leave that up to you.
>
> Oh I would be happy to get one with the components as well! How can we get in touch to get this organised?

Me too :))

C44Supra, 2022-03-28:
I should have about 3 spares as I'm looking to keep 2 for myself. In hindsight, probably should've ordered a few more PCBs. Either way, don't want to step on @scottbez1's toes, if he's okay with me charging a little bit of money for assembly on top of PCB + parts + shipping, we can go ahead.

18Markus1984, 2022-03-28:
> I should have about 3 spares as I'm looking to keep 2 for myself. In hindsight, probably should've ordered a few more PCBs. Either way, don't want to step on @scottbez1's toes, if he's okay with me charging a little bit of money for assembly on top of PCB + parts + shipping, we can go ahead.
>
> That said, I'm still waiting for the ESPs to come in. According to AliExpress shipping that should be this week. Once those are here I should have all the parts needed for PCBA.

Yes, that would be pretty nice. I will definitly pay you for this. My mail is markusschmidt1984@gmx.de

zablotzky, 2022-03-28:
From experience with other projects devs usually have nothing against it, as long as feedback is provided to keep track of all the issues. Drop me an email at jacek dot zablocki at outlook dot com to push things forward :)

Horia73, 2022-03-28:
> I should have about 3 spares as I'm looking to keep 2 for myself. In hindsight, probably should've ordered a few more PCBs. Either way, don't want to step on @scottbez1's toes, if he's okay with me charging a little bit of money for assembly on top of PCB + parts + shipping, we can go ahead.
>
> That said, I'm still waiting for the ESPs to come in. According to AliExpress shipping that should be this week. Once those are here I should have all the parts needed for PCBA.

I will definitely  pay you. My email is iugahoria@gmail.com
If @scottbez1 it s okay with this of course.

C44Supra, 2022-03-28:
@18Markus1984 @zablotzky @Horia73 Sent you guys some emails.

That motor does indeed look to be the same one. Never heard of that specific site before though. I they have stock, it's likely limited though. I'm currently in touch with a manufacturer for possible replacement motors as per #16

C44Supra, 2022-03-28:
Looks to only ship within India as well, that could be an issue for anyone outside of India.

scottbez1, 2022-03-28:
> don't want to step on @scottbez1's toes, if he's okay with me charging a little bit of money for assembly on top of PCB + parts + shipping, we can go ahead.

Go for it - that's the beauty of open source!

18Markus1984, 2022-03-28:
> @18Markus1984 There's a ticket for the motor stocking issue already: #16 PCBs shouldn't be that expensive, you can get them made for a couple of dollars and shipped for a few more dollars at JLC. All depends on how patient you are.

18Markus1984, 2022-03-28:
> @18Markus1984 There's a ticket for the motor stocking issue already: #16 PCBs shouldn't be that expensive, you can get them made for a couple of dollars and shipped for a few more dollars at JLC. All depends on how patient you are.

Extra looked over all the tickets, but sadly I missed it  😅

18Markus1984, 2022-05-08:
> @18Markus1984 @zablotzky @Horia73 Sent you guys some emails.
>
> That motor does indeed look to be the same one. Never heard of that specific site before though. I they have stock, it's likely limited though. I'm currently in touch with a manufacturer for possible replacement motors as per #16

I accidentally deleted your mail and didn't find a better way to ask when I could pay you for the PCBs?

Closed 2022-03-28.

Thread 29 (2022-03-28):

can't find ESP32 when upload firmware to base board.

zinwalin, 2022-03-28:
Building in release mode
Retrieving maximum program size .pio\build\view\firmware.elf
Checking size .pio\build\view\firmware.elf
Advanced Memory Usage is available via "PlatformIO Home > Project Inspect"
RAM:   [=         ]   5.4% (used 17648 bytes from 327680 bytes)
Flash: [===       ]  27.3% (used 357450 bytes from 1310720 bytes)
Configuring upload protocol...
AVAILABLE: esp-prog, espota, esptool, iot-bus-jtag, jlink, minimodule, olimex-arm-usb-ocd, olimex-arm-usb-ocd-h, olimex-arm-usb-tiny-h, olimex-jtag-tiny, tumpa
CURRENT: upload_protocol = esptool
Looking for upload port...
Auto-detected: COM3
Uploading .pio\build\view\firmware.bin
esptool.py v3.1
Serial port COM3
Connecting........_____....._____....._____....._____....._____....._____....._____

A fatal error occurred: Failed to connect to ESP32: Timed out waiting for packet header
*** [upload] Error 2
================================================================================================================================ [FAILED] Took 28.07 seconds ================================================================================================================================
Environment    Status    Duration
-------------  --------  ------------
view           FAILED    00:00:28.074
=========================================================================================================================== 1 failed, 0 succeeded in 00:00:28.074 ===========================================================================================================================The terminal process "C:\Users\zinwa\.platformio\penv\Scripts\platformio.exe 'run', '--target', 'upload', '--environment', 'view'" terminated with exit code: 1.

Terminal will be reused by tasks, press any key to close it.

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

scottbez1, 2022-03-28:
It looks like Q2 is not populated, which is the dual transistor package that provides the reset and boot mode selection via USB serial DTR and RTS, so automatic downloads won't work without that.

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

You can use the solder pads for EN and BOOT on the bottom to manually put the chip into program mode - connect BOOT to ground, then start the upload, then briefly connect EN to ground while you see the Connecting..... message.

zinwalin, 2022-03-28:
>

@scottbez1 Hi Scott, thanks for your reply, Q2 component is not shipped out yet, I used EN and BOOT to flash once successfully, it's quite tricky.   BTW, where did you find the picture you referred in your reply?

scottbez1, 2022-03-28:
Awesome, glad you were able to get it working! That photo is from the [schematic](https://smartknob-artifacts.s3.us-west-1.amazonaws.com/refs/tags/releases/view_base/v0.4/electronics/view_base-schematic.pdf) which can be found linked from the [releases](https://github.com/scottbez1/smartknob/releases) or on the main README (for the latest bleeding edge version)

Closed 2022-03-28.

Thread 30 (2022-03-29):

Can you upload real photos for your soldered PCB boards?

zinwalin, 2022-03-29:
I purchased components from online shop, when soldering it's quite tricky to get the right direction for LEDs, need your PCB boards for reference. Appreciated for your efforts.

C44Supra, 2022-03-29:
There are links in the Readme to the InteractiveHTMLBOM for both the main PCB (https://smartknob-artifacts.s3.us-west-1.amazonaws.com/master/electronics/view_base-ibom.html) and the screen PCB (https://smartknob-artifacts.s3.us-west-1.amazonaws.com/master/electronics/view_screen-ibom.html). If you press the gear icon in the top right of the page and select the option "Highlight first pin", that will show you part polarization.

Most of the components speak for themselves, but for LEDs and diodes in general, pin one is cathode. Resistors and caps are non-polarized so no worries there.

scottbez1, 2022-03-29:
If you haven't already, I'd recommend opening the [view_base](https://github.com/scottbez1/smartknob/tree/59420c6da924c546f69fda3c9bdcbbe309c0524d/electronics/view_base) project in KiCad and using the built-in 3d viewer to look around. I took care to make sure as many components as possible had accurate 3d models associated with them so the render should be very accurate.

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

Alternatively, the main [3d mechanical cad file](https://a360.co/3BzkU0n) includes a semi-recent export of that PCB 3d model, so you can use Autodesk's web-based 3d viewer to look around at the PCB.

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

Let me know if you still have questions after checking out those tools, and I can snap some photos of specific areas if there's something that's not clear.

zinwalin, 2022-03-30:
>

Thanks.  U1, U3, U4, U5 have polarized restriction, I made mistake for U5 at first soldering, and when powered, TMC6300 is so hot. After change the direction, it works.

Closed 2022-03-30.

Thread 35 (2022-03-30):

Without screen PCB, how can I test features?

zinwalin, 2022-03-30:
I didn't receive all components, no strain gauge at the moment, when I touch pins on strain gauge position, the mode is changed.

--------------------------------------------
Please build project in debug configuration to get more details about an exception.
See https://docs.platformio.org/page/projectconf/build_configurations.html

--- Miniterm on COM3  115200,8,N,1 ---
--- Quit: Ctrl+C | Menu: Ctrl+T | Help: Ctrl+T followed by Ctrl+H ---
ets Jul 29 2019 12:21:46

rst:0x1 (POWERON_RESET),boot:0x13 (SPI_FAST_FLASH_BOOT)
configsip: 271414342, SPIWP:0xee
clk_drv:0x00,q_drv:0x00,d_drv:0x00,cs0_drv:0x00,hd_drv:0x00,wp_drv:0x00
mode:DIO, clock div:2
load:0x3fff0018,len:4
load:0x3fff001c,len:1044
load:0x40078000,len:10124
load:0x40080400,len:5828
entry 0x400806a8
use SENSOR_MT6701
MOT: Monitor enabled!
MOT: Init
MOT: Enable driver.
millilux: 165384.00
MOT: Align sensor.
MOT: Skip dir calib.
MOT: Skip offset calib.
millilux: 165470.39
MOT: No current sense.
MOT: Ready.
Press Y to run calibration
millilux: 165484.80
millilux: 165484.80
millilux: 165441.61
7.34
Got new config
millilux: 165441.61
millilux: 165441.61
millilux: 165441.61
----------------------------------------------------
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

scottbez1, 2022-03-30:
Closing in favor of #36

Closed 2022-03-30.

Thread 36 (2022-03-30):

How to detect wheter motor and driver is working properly?

zinwalin, 2022-03-30:
I used TMC6300 and 3215 motor, looks like there's no torque when base PCB is powered.

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

zinwalin, 2022-03-30:
Looks like the motor is not working at all.

---------------------

--- Miniterm on COM5  115200,8,N,1 ---
--- Quit: Ctrl+C | Menu: Ctrl+T | Help: Ctrl+T followed by Ctrl+H ---
ets Jul 29 2019 12:21:46

rst:0x1 (POWERON_RESET),boot:0x13 (SPI_FAST_FLASH_BOOT)
configsip: 271414342, SPIWP:0xee
clk_drv:0x00,q_drv:0x00,d_drv:0x00,cs0_drv:0x00,hd_drv:0x00,wp_drv:0x00
mode:DIO, clock div:2
load:0x3fff0018,len:4
load:0x3fff001c,len:1044
load:0x40078000,len:10124
load:0x40080400,len:5828
entry 0x400806a8
MotorTask::run()
MOT: Monitor enabled!
MOT: Init
MOT: Enable driver.
millilux: 2340.00
MOT: Align sensor.
MOT: Skip dir calib.
MOT: Skip offset calib.
millilux: 2318.40
MOT: No current sense.
MOT: Ready.
Press Y to run calibration
millilux: 2433.60
millilux: 2534.40
millilux: 2599.20
2.93
Got new config
millilux: 2548.80
millilux: 2577.60
millilux: 2577.60
millilux: 2599.20
millilux: 2592.00

scottbez1, 2022-03-30:
Have you run calibration yet? Press Y in the serial monitor when you see the "Press Y to run calibration" message at startup (you have to be somewhat quick). This will run through a few open-loop movements of the motor (that don't require any other sensors or components to work correctly, unlike normal operation).

If the motor doesn't work during that, then you'll need to debug further - probably best to oscillocope probe the UVW test points on the bottom for that, to see if there is any voltage coming out of the TMC6300. You could also probe R7-R12 to verify that the correct signals for UL/UH/VL/VH/WL/WH are being output by the ESP32.

But also, in #34 you mentioned that the TMC6300 got very hot due to being soldered in the wrong orientation - did you replace that chip with a fresh one, or just rotate it?

zinwalin, 2022-03-31:
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

Hi Scott, when goes into calibration, the fireware crashed and base PCB reboot.  In terms of TMC6300, I only rotate chip to make it run without hot.

Here's the crash log when calibration.

--- Miniterm on COM6  115200,8,N,1 ---
--- Quit: Ctrl+C | Menu: Ctrl+T | Help: Ctrl+T followed by Ctrl+H ---
ets Jul 29 2019 12:21:46

rst:0x1 (POWERON_RESET),boot:0x13 (SPI_FAST_FLASH_BOOT)
configsip: 271414342, SPIWP:0xee
clk_drv:0x00,q_drv:0x00,d_drv:0x00,cs0_drv:0x00,hd_drv:0x00,wp_drv:0x00
mode:DIO, clock div:2
load:0x3fff0018,len:4
load:0x3fff001c,len:1044
load:0x40078000,len:10124
load:0x40080400,len:5828
entry 0x400806a8
millilux: 3132.00
MT6701 getSensorAngle...
0.15
millilux: 3124.80
Press Y to run calibration
millilux: 3153.60
millilux: 3225.60
millilux: 3304.80
millilux: 3355.20
millilux: 3384.00
millilux: 3484.80

Sensor measures positive for positive motor rotation: NO, Direction=CCW
millilux: 3564.00
Guru Meditation Error: Core  1 panic'ed (Unhandled debug exception)
Debug exception reason: Stack canary watchpoint triggered (Motor)
Core 1 register dump:
PC      : 0x400db5d1  PS      : 0x00060c36  A0      : 0x800e0d35  A1      : 0x3ffb8280
A2      : 0x00000000  A3      : 0x00000011  A4      : 0x00000001  A5      : 0x3f4003b8
A6      : 0x3ffb8660  A7      : 0x00000008  A8      : 0x3f4003a7  A9      : 0x3ffb8474
A10     : 0x3ffb8290  A11     : 0x3ff9c510  A12     : 0x000000ff  A13     : 0x0000ff00
A14     : 0x00ff0000  A15     : 0xff000000  SAR     : 0x0000001d  EXCCAUSE: 0x00000001
EXCVADDR: 0x00000000  LBEG    : 0x400014fd  LEND    : 0x4000150d  LCOUNT  : 0xffffffff

ELF file SHA256: 0000000000000000

Backtrace: 0x400db5d1:0x3ffb8280 0x400e0d32:0x3ffb8590 0x400e0d6a:0x3ffb8620 0x400d6672:0x3ffb8660 0x400d2808:0x3ffb8700 0x400d22a9:0x3ffb8850 0x40088211:0x3ffb8870
  #0  0x400db5d1:0x3ffb8280 in _svfprintf_r at /Users/ivan/e/newlib_xtensa-2.2.0-bin/newlib_xtensa-2.2.0/xtensa-esp32-elf/newlib/libc/stdio/../../../.././newlib/libc/stdio/vfprintf.c:929
  #1  0x400e0d32:0x3ffb8590 in _vsnprintf_r at /Users/ivan/e/newlib_xtensa-2.2.0-bin/newlib_xtensa-2.2.0/xtensa-esp32-elf/newlib/libc/stdio/../../../.././newlib/libc/stdio/vsnprintf.c:72
  #2  0x400e0d6a:0x3ffb8620 in vsnprintf at /Users/ivan/e/newlib_xtensa-2.2.0-bin/newlib_xtensa-2.2.0/xtensa-esp32-elf/newlib/libc/stdio/../../../.././newlib/libc/stdio/vsnprintf.c:41
  #3  0x400d6672:0x3ffb8660 in Print::printf(char const*, ...) at C:\Users\zinwa\.platformio\packages\framework-arduinoespressif32\cores\esp32/Print.cpp:254
  #4  0x400d2808:0x3ffb8700 in MotorTask::run() at src/motor_task.cpp:163
  #5  0x400d22a9:0x3ffb8850 in Task<MotorTask>::taskFunction(void*) at src/task.h:46
  #6  0x40088211:0x3ffb8870 in vPortTaskWrapper at /home/runner/work/esp32-arduino-lib-builder/esp32-arduino-lib-builder/esp-idf/components/freertos/port.c:355 (discriminator 1)

Rebooting...
ets Jul 29 2019 12:21:46

zinwalin, 2022-03-31:
BTW, another question for TMC6300, how to check whether it is detected or is running well?

zinwalin, 2022-03-31:
>
Hi Scott, good news for the issue, after checkc R7-R12, and U/V/W for motor, ESP32 output is normal, U/V/W is zero, so I replaced a new TMC6300, and it is powered, the motor moves.   Brilliant, thanks for your tips.

Closed 2022-03-31.

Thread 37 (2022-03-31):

crash when run calibration with typing Y

zinwalin, 2022-03-31:
--- Miniterm on COM6  115200,8,N,1 ---
--- Quit: Ctrl+C | Menu: Ctrl+T | Help: Ctrl+T followed by Ctrl+H ---
ets Jul 29 2019 12:21:46

rst:0x1 (POWERON_RESET),boot:0x13 (SPI_FAST_FLASH_BOOT)
configsip: 271414342, SPIWP:0xee
clk_drv:0x00,q_drv:0x00,d_drv:0x00,cs0_drv:0x00,hd_drv:0x00,wp_drv:0x00
mode:DIO, clock div:2
load:0x3fff0018,len:4
load:0x3fff001c,len:1044
load:0x40078000,len:10124
load:0x40080400,len:5828
entry 0x400806a8
Sprite created!
millilux: 26236.80
millilux: 26949.60
Press Y to run calibration
Ymillilux: 26942.40
millilux: 27057.60
millilux: 26697.60
millilux: 27021.60

Sensor measures positive for positive motor rotation: YES, Direction=CW
Guru Meditation Error: Core  1 panic'ed (Unhandled debug exception)
Debug exception reason: Stack canary watchpoint triggered (Motor)
Core 1 register dump:
PC      : 0x400dfaf1  PS      : 0x00060c36  A0      : 0x800e5255  A1      : 0x3ffb8280
A2      : 0x00000000  A3      : 0x00000011  A4      : 0x00000001  A5      : 0x3f404396
A6      : 0x3ffb8660  A7      : 0x00000008  A8      : 0x3f404385  A9      : 0x3ffb8474
A10     : 0x3ffb8290  A11     : 0x3ff9c510  A12     : 0x000000ff  A13     : 0x0000ff00
A14     : 0x00ff0000  A15     : 0xff000000  SAR     : 0x0000001d  EXCCAUSE: 0x00000001
EXCVADDR: 0x00000000  LBEG    : 0x400014fd  LEND    : 0x4000150d  LCOUNT  : 0xffffffff

ELF file SHA256: 0000000000000000

Backtrace: 0x400dfaf1:0x3ffb8280 0x400e5252:0x3ffb8590 0x400e528a:0x3ffb8620 0x400da4ca:0x3ffb8660 0x400d3280:0x3ffb8700 0x400d2ced:0x3ffb8850 0x400883f2:0x3ffb8870
  #0  0x400dfaf1:0x3ffb8280 in _svfprintf_r at /Users/ivan/e/newlib_xtensa-2.2.0-bin/newlib_xtensa-2.2.0/xtensa-esp32-elf/newlib/libc/stdio/../../../.././newlib/libc/stdio/vfprintf.c:929
  #1  0x400e5252:0x3ffb8590 in _vsnprintf_r at /Users/ivan/e/newlib_xtensa-2.2.0-bin/newlib_xtensa-2.2.0/xtensa-esp32-elf/newlib/libc/stdio/../../../.././newlib/libc/stdio/vsnprintf.c:72
  #2  0x400e528a:0x3ffb8620 in vsnprintf at /Users/ivan/e/newlib_xtensa-2.2.0-bin/newlib_xtensa-2.2.0/xtensa-esp32-elf/newlib

scottbez1, 2022-04-07:
It looks like this is probably the same issue as in #50 - can you try the fix suggested here: https://github.com/scottbez1/smartknob/issues/50#issue-1195172430

scottbez1, 2022-04-07:
Closing since I'm pretty sure this was the same issue as #50 and should be fixed in e35319a. Please let me know if increasing the stack size didn't fix it though.

zinwalin, 2022-04-10:
@scottbez1 the commit https://github.com/scottbez1/smartknob/commit/e35319af6d4223d03087177da39b63936b2836fb didn't fix the issue.

----

Sensor measures positive for positive motor rotation: YES, Direction=CW
millilux: 78379.20
Guru Meditation Error: Core  1 panic'ed (Unhandled debug exception)
Debug exception reason: Stack canary watchpoint triggered (Motor)
Core 1 register dump:
PC      : 0x400dfb19  PS      : 0x00060c36  A0      : 0x800e527d  A1      : 0x3ffb8280
A2      : 0x00000000  A3      : 0x00000011  A4      : 0x00000001  A5      : 0x3f404463
A6      : 0x3ffb8660  A7      : 0x00000008  A8      : 0x3f404452  A9      : 0x3ffb8474
A10     : 0x3ffb8290  A11     : 0x3ff9c510  A12     : 0x000000ff  A13     : 0x0000ff00
A14     : 0x00ff0000  A15     : 0xff000000  SAR     : 0x0000001d  EXCCAUSE: 0x00000001
EXCVADDR: 0x00000000  LBEG    : 0x400014fd  LEND    : 0x4000150d  LCOUNT  : 0xffffffff

ELF file SHA256: 0000000000000000

Backtrace: 0x400dfb19:0x3ffb8280 0x400e527a:0x3ffb8590 0x400e52b2:0x3ffb8620 0x400da4f2:0x3ffb8660 0x400d32cc:0x3ffb8700 0x400d2d01:0x3ffb8850 0x400883f2:0x3ffb8870
  #0  0x400dfb19:0x3ffb8280 in _svfprintf_r at /Users/ivan/e/newlib_xtensa-2.2.0-bin/newlib_xtensa-2.2.0/xtensa-esp32-elf/newlib/libc/stdio/../../../.././newlib/libc/stdio/vfprintf.c:929
  #1  0x400e527a:0x3ffb8590 in _vsnprintf_r at /Users/ivan/e/newlib_xtensa-2.2.0-bin/newlib_xtensa-2.2.0/xtensa-esp32-elf/newlib/libc/stdio/../../../.././newlib/libc/stdio/vsnprintf.c:72
  #2  0x400e52b2:0x3ffb8620 in vsnprintf at /Users/ivan/e/newlib_xtensa-2.2.0-bin/newlib_xtensa-2.2.0/xtensa-esp32-elf/newlib/libc/stdio/../../../.././newlib/libc/stdio/vsnprintf.c:41
  #3  0x400da4f2:0x3ffb8660 in Print::printf(char const*, ...) at C:\Users\zinwa\.platformio\packages\framework-arduinoespressif32\cores\esp32/Print.cpp:254
  #4  0x400d32cc:0x3ffb8700 in MotorTask::run() at src/motor_task.cpp:159
  #5  0x400d2d01:0x3ffb8850 in Task<MotorTask>::taskFunction(void*) at src/task.h:46
  #6  0x400883f2:0x3ffb8870 in vPortTaskWrapper at /home/runner/work/esp32-arduino-lib-builder/esp32-arduino-lib-builder/esp-idf/components/freertos/port.c:355 (discriminator 1)

Rebooting...
ets Jul 29 2019 12:21:46

Closed 2022-04-07.

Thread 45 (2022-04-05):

[Imporvement] Hard to fix the LCD screen in the knob

zinwalin, 2022-04-05:
See the pciture depicted below, the screen moved when I assembled, there's not slot to fix the screen.

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

scottbez1, 2022-04-07:
Hmmm, which part came loose - was it the joint between the MountBase and ScreenPlatform 3d printed parts, or was it the joint between the ScreenPlatform and the screen PCB?

In general there should not be any interference as long as the screen PCB assembly was assembled within tolerance (i.e. using 0.6mm VHB tape rather than the more common 1.1mm variant, making sure the LCD is fully attached to the PCB with no gaps from the wires, etc). Then as long as you are careful to align the spokes of the RotorSpacer to avoid the ribbon cable "chin" on the LCD when assembling, everything should fit together without issue.

If you used mechanical parts prior to v185, the gap between the LCD and the inside of the Knob was slightly too small, causing potential rubbing when the knob is rotated, but this would not have been enough to dislodge the LCD assembly. An additional 0.5mm gap between LCD and knob was added in the v185 release to account for that potential issue.

willumpie82, 2022-04-19:
dit you consider using a piece of brass tube and just solder that to upper and lower boards (perferable with dualsided exposed copper on the boards for rigidity)?

willumpie82, 2022-05-12:
simple proof of concept with a 5mm brass tube, I'll try to create a version of the boards to have a coper area to solder the shaft on, a bit of grease can be added to smooth the rotation, there is about .15mm clearance between the shaft and the motor hollow shaft radius
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

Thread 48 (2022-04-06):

How to check whether HX711/Strain gauges has problem?

zinwalin, 2022-04-06:
It's not working on my side, before fixed strain gauges on PCB, I just want to validate strain gauges is originally working with HX711.

There's current on 6 pads for strain gauges, but no response(the screen keeps showing Unbounded No detents which is the mode by defaut) when I touched 4 strain gauges when powered.

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

scottbez1, 2022-04-07:
The strain gauge thresholds will need to be manually calibrated based on your physical assembly (every build will be different).

The code outputs a `HX711 reading` value to the serial console once per second by default. You can check that this changes when you touch a strain gauge.

Then once the strain gauges are permanently installed, you can get a reading when nothing is pressed and set this as the "lower" value, and then press down on the knob and get a reading there and set that as the "upper" value here: https://github.com/scottbez1/smartknob/blob/5c2a10428a7c4736a4aa2c93c831fbd3f2271b72/firmware/src/interface_task.cpp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

scottbez1, 2022-04-07:
Also, by the way, for testing the knob without the strain gauges, you can press [space] in the serial monitor to switch to the next mode in lieu of activating the strain gauges.

zinwalin, 2022-04-07:
> Also, by the way, for testing the knob without the strain gauges, you can press [space] in the serial monitor to switch to the next mode in lieu of activating the strain gauges.

Yes. I get used to press space to change mode.

zinwalin, 2022-04-07:
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

Hi Scott, your reply saved lots of time, there's no console output for HX711 reading by default, cause the lower and upper values are too high on my side, so the logic for HX711 is not run.  After I lower the values, it works.  Appreciated for your reminders.

scottbez1, 2022-04-07:
Glad to have helped!

Closed 2022-04-07.

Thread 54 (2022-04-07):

Free up memory to enable wifi or bluetooth

scottbez1, 2022-04-07:
Currently there is not enough memory available to initialize wifi (and I assume the same is likely true of bluetooth though I haven't tested yet).

A big culprit is the full 240x240x16b framebuffer in the display task which is used to avoid flickering when rendering. Two ideas of avoiding this memory issue:
- potentially enable PSRAM (the ESP32-PICO-V3-02 has 2MB SPI PSRAM built in but not enabled by default in the current Arduino core). I did an initial test trying to enable PSRAM by using a newer arduino platform from git, but overall CPU performance ended up really bad. I didn't dig further where that performance hit was coming from, so I'm not sure if whether this approach is viable or not
- migrate the graphics to LVGL, which supposedly can work with a smaller buffer and do tiled rendering (and do smarter rendering if regions haven't changed). I haven't used LVGL before, but it looks pretty powerful, and should also simplify adding things like a menu system later

There are some other memory issues, like the default arduino loop task allocates a (fixed) moderately sized stack but is essentially completely unused and gets deleted immediately after starting other tasks, but I think those issues are smaller scale compared to the framebuffer issue.

mcmadhatter, 2022-04-07:
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
LVGL is something I have been trying out whilst I wait for some motors I’ve ordered to arrive. The above is running on a modified version of the handheld branch. It creates a new task called UI_Task, to contain all of the lvgl requests. Under the hood lvgl uses TFT_eSPI. There is not much there yet as I am still playing with the configuration

zinwalin, 2022-04-07:
> 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
>
> LVGL is something I have been trying out whilst I wait for some motors I’ve ordered to arrive. The above is running on a modified version of the handheld branch. It creates a new task called UI_Task, to contain all of the lvgl requests. Under the hood lvgl uses TFT_eSPI. There is not much there yet as I am still playing with the configuration

Good progress.

zinwalin, 2022-04-07:
@scottbez1 Hi Scott. I found esp32 we use has 8MB flash and 2MB PSRAM. But the log shows incorrectly.

PLATFORM: Espressif 32 (3.4.0) > DOIT ESP32 DEVKIT V1
HARDWARE: ESP32 240MHz, 320KB RAM, 4MB Flash

jtsfour, 2022-04-07:
@zinwalin Sorry to be off-topic.  What board are you using with that small display?  I would also like to tinker before I can get motors.

scottbez1, 2022-04-07:
@jtsfour That's a Lilygo T-Display - it's a great ESP32 board, and there's even a [pio env](https://github.com/scottbez1/smartknob/blob/e35319af6d4223d03087177da39b63936b2836fb/firmware/platformio.ini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) set up to use it for prototyping the smartknob as well! (though since I haven't done much prototyping with it recently, it's possible that T-Display env hasn't quite kept up to date, but it should at least compile)

It also happens to be the board I recommend using for my [splitflap](https://github.com/scottbez1/splitflap) project

zinwalin, 2022-04-07:
> @zinwalin Sorry to be off-topic.  What board are you using with that small display?  I would also like to tinker before I can get motors.

I mean T-Micro32 Plus has 8MB flash and 2MB PSRAM.

scottbez1, 2022-04-08:
When I initially set up the project, the stable Arduino core yet didn't have support for using the PSRAM on the ESP32-PICO-V3-02, so that is not expected to show up as available. More info here: https://community.platformio.org/t/support-for-eps32-pico-v3/26967

It looks like it's still not landed, but I'm hopeful that there will be an official release soon. Otherwise I guess we can switch to the Jason2866 platform to get PSRAM support sooner.

AR17HY, 2022-05-27:
You could try the following code to check if you have 8Mb Flash (I don't have this version) :

```
void GetChipAndMemoryDetails (void)
{
// This function display the details of the integrated chip (memory, core, bluetooth)
// It also give external memory size
    /* Print chip information */
    Serial.println();
    esp_chip_info_t chip_info;
    esp_chip_info(&chip_info);
    Serial.printf("This is ESP32 chip with %d CPU cores, WiFi%s%s, ",
                  chip_info.cores,
                  (chip_info.features & CHIP_FEATURE_BT) ? "/BT" : "",
                  (chip_info.features & CHIP_FEATURE_BLE) ? "/BLE" : "");
    Serial.println();
    Serial.printf("silicon revision %d, ", chip_info.revision);
    Serial.println();
    Serial.printf("%dMB %s flash\n", spi_flash_get_chip_size() / (1024 * 1024),
                  (chip_info.features & CHIP_FEATURE_EMB_FLASH) ? "embedded" : "external");
}
```

I believe there is no PSRAM (external component) on this board and it is not supported by the MCU used by espressif on this specific board (PIN 16 and 17 dedicated in Wroover modules version to support PSRAM).

septatrix, 2022-06-24:
The Arduino Core for ESP32 simply uses the esp-idf/FreeRTOS under the hood. Using it directly opens up [*a lot of* optimizations](https://docs.espressif.com/projects/esp-idf/en/latest/esp32/api-guides/performance/ram-usage.html) for reducing RAM usage by the FreeRTOS itself and also the Wifi stack (e.g. how large the buffers should be and the maximum amount of connections).
This would obviously require some refactoring but large parts of the code already use functions from FreeRTOS so added complexity is rather small. Some other tweaks could be made by reducing the stack size for tasks and maybe using static allocation where possible. Oh and obviously it would support PSRAM though that might be too slow for the framebuffer itself.

lgc00, 2022-08-04:
Not sure if it was mentioned anywhere but you can reduce color depth to 8 bit from 16 bit and reduce memory usage for sprite by half - according to the documentation for `createSprite` method in `TFT_eSprite`, 8 bit color requires 1 byte per pixel compared to 2 bytes for 16 bit color. Unless you absolutely need 16 bit color depth, this seems to be a nice trade off for now.

I changed color depth value in `display_task.cpp` with `spr_.setColorDepth(8);` and was able to initialize wifi, connect to mqtt and send out test message just fine, no memory issues.

wlzxzq, 2022-09-22:
> wifi

how tu get your modified project, can you share your code

wlzxzq, 2022-09-22:
maybe the device can use two core. auther maybe use one core

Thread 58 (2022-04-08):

Idea: Use a capacitive touch screen display

rtbcoop, 2022-04-08:
If you use a touch screen display, you would no longer need the strain gauge.  You would also open up a lot of new capabilities such as gesture controls.

scottbez1, 2022-04-08:
Yeah, that would definitely be cool! I considered it and intentionally omitted it from this first iteration for 2 reasons:
- There are some really nice looking high dpi AMOLED displays based on the RM69330 driver IC from smartwatches that can be found for < US$20 with built in capacitive digitizers, but they have 4x the total pixel count (which may make them tricky to drive with an ESP32's limited memory) and there isn't yet open-source driver support in e.g. TFT_eSPI. Some discussion can be found [here](https://www.eevblog.com/forum/microcontrollers/driving-a-round-amoled-display/msg3757085/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). I'm also not sure how readily available these are or if there's just excess stock that will disappear quickly.
- mechanically things get more complex, since the screen now needs to sit *above* the knob/rotor, rather than the current approach where there's a watch crystal directly attached to the knob/rotor that rotates with it. This means there needs to be an external gap between the display and the rest of the knob/rotor, which I think would be tricky to make look good especially with 3d-printing and manual assembly tolerances

rtbcoop, 2022-04-08:
I am sure there are others that are better suited to solve the electrical issue, but I can definitely solve the mechanical issue.  Instead of using a hollow shaft motor, I'd mount the knob to two captured bearings and then drive the knob with gears instead of directly off the motor.  This would:
1. Give you much better resolution (more steps per rotation of the knob thanks to gearing)
2. Give you more motor options since you aren't limited to hollow shaft motors
3. Provide more internal room for supports and wire runs.

These should all be commercial off the shelf parts that wouldn't add too much complexity or cost.  I'm glad to do the mechanical design legwork if this is a road you'd be interested in going down.  I'll post this up in Issue 16 as well to see if anyone has feedback.

DavidClawson, 2022-04-08:
I would wonder about the sensory feel of the drive gears. If the ratios were too high, it might be hard or strange to drive them by turning (vs a brushless which offers essentially zero resistance when not energized). You might also have issues with backlash, but maybe not too big of a deal.

hofstee, 2022-04-08:
> 1. Give you much better resolution (more steps per rotation of the knob thanks to gearing)

Magnetic encoders will already get you <0.1 degree usable resolution so I'm not sure having more than that will be meaningfully useful.

rtbcoop, 2022-04-09:
> I would wonder about the sensory feel of the drive gears. If the ratios were too high, it might be hard or strange to drive them by turning (vs a brushless which offers essentially zero resistance when not energized). You might also have issues with backlash, but maybe not too big of a deal.

Valid concern.  I don't think it would be terrible if you kept the gear ratio low.  That would take some testing.

> Magnetic encoders will already get you <0.1 degree usable resolution so I'm not sure having more than that will be meaningfully useful.

True, I don't think the added resolution would have any benefit on the sensing side, but I think it would make a difference on the feedback side.  You could have much finer detents and a smoother knob resistance.

rtbcoop, 2022-04-09:
This is what I had in mind.  In the real design, I would mount the gears to the bottom of the knob; this design was just for a visual.

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

psyspy1, 2022-04-10:
@scottbez1 About your first point of the RM69330 touch screen display having higher pixel count and needing more memory, wouldn't [this](https://www.buydisplay.com/240x240-round-ips-tft-lcd-display-1-28-inch-capactive-touch-circle-screen) display work? It uses the same driver GC9A01A and seems to have the same dimensions and pixel count as the current one.

EUA, 2023-01-27:
Capacitive/Resistive touchscreen will also make **AC/DC converter and flex gauge sensors obsolete**. Make project easier and probably cheaper to build...

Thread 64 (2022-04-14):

Idea: use a Raspberry Pi 2W board

radu-boboc, 2022-04-14:
I know we got  bigger issues right now, with missing motors but I was thinking that if this project is to have success above the cool factor of the knob, then it needs to be able to do stuff like integrate into project's.
I understood from reading the issues that we don't have enough memeory available to import WiFi libraries.
So that means no connectivity to real projects.

So I propose to use instead the much more powerful Raspberry Pi 2W board. It has lots of memory, lot's of storage, good WiFi and Bluetooth connectivity and lots of IO pins.
There are two options integrate the board: directly by making a pinout holes on the PCB, or just solder the chip that can be bought separately.

What do you think of this migrate to Raspberry Pi proposition?

dylmeistah, 2022-04-21:
I feel like this could work, but a proof of concept would first be needed to call this a viable solution.

vlad-the-compiler, 2022-04-30:
I personally think this would be overkill for such a project, especially since it's an input device, and you shouldn't have to wait for a peripheral to boot a full-fledged Linux OS after you plug it in.

This is the type of project where the best fit is a microcontroller.

ghamauricio, 2022-04-30:
> I personally think this would be overkill for such a project, especially since it's an input device, and you shouldn't have to wait for a peripheral to boot a full-fledged Linux OS after you plug it in.
>
> This is the type of project where the best fit is a microcontroller.

I totally agree.

Actually, I would really love to use this knob in my lighting controller project based on Arduinos and Arduino-compatible boards!

vlad-the-compiler, 2022-05-02:
> If anything the main board should be more focused, providing a USB HID and maybe a Bluetooth HID device, but no wifi

This sounds like the task for an nRF52840, which has Arduino support through their own Nano 33 BLE/Sense boards, or Seeed's small form factor 'Xiao nRF52' boards.
ESP32 support should still be a thing however, since a project like this is perfect for being adapted into a wall-mounted IoT controller.

radu-boboc, 2022-05-02:
> I personally think this would be overkill for such a project, especially since it's an input device, and you shouldn't have to wait for a peripheral to boot a full-fledged Linux OS after you plug it in.
>

I also agree, it would be overkill and having a 10 second boot time to a cool button is not what we expect.
BUT!
We don't boot everyday and that 10 seconds could be once / year, and perhaps optimized a lot, by cutting down unnecessary stuff from the OS.

Also a Raspberry Pi would give the opportunity to do **stuff** with this button.
In the present configuration, with no WiFi, it is only a gimmick. Because of no connectivity, there is no other real world use other then a nice toy to show your friends.
If you want to integrate it with any of your projects, it should have WiFi + Bluetooth, plus space for some other software that we will write in the future.
As for cost, adding 10-15$ to a 100-200 button, is not so much. ( _actually less, because you will also remove the esp32_ ) and if we integrate it via SOC ( not board), it will cost even less.

I would argue that the benefits out-way the inconveniences so I keep my suggestion of making it useful and future proof.

ghamauricio, 2022-05-02:
> In the present configuration, with no WiFi, it is only a gimmick. Because of no connectivity, there is no other real world use other then a nice toy to show your friends.

Sure, hook it up to your Raspberry Pi using UART, SPI, I2C or any other communication method you want.

This is an HID device, and I agree it shouldn't be asked to do much more then HID stuff. If you want more functionality, add it yourself. That's what's expected from all of us who want to integrate such a neat little HID device into our projects.

vlad-the-compiler, 2022-05-03:
> Also a Raspberry Pi would give the opportunity to do stuff with this button.
In the present configuration, with no WiFi, it is only a gimmick. Because of no connectivity, there is no other real world use other then a nice toy to show your friends.

The current configuration is based on an ESP32, which has BT/BLE and Wi-Fi capabilities. It also is fast enough to provide a proper user interface on the display. It comes equipped with all of the interfaces you'd want, except for native USB - but that is supported on the S3 revision of the chip. Honestly, ESP32 is the perfect application processor for such a device, if we're to abide by the single responsibility principle.

ESP32 just makes a lot of sense for this particular project. A full-fledged computer? I fail to see a situation in which that would be needed. Nobody ever complains about their computer mouse having a 64MHz STM32 as their application processor, and for good reason.

k1-801, 2022-05-09:
Instead of a Raspberry Pi 2W, I'd suggest using a Raspberry Pi Compute Module, probably the latest cm4. The scenario where it could come in handy is a camera-based access control, with a camera (or two) mounted close to a corner of the outer case (two top corners in case of two cameras), and connected to the CM via CSI. However, in this scenario, the board will be under a heavy CPU load for image processing, and thus, a secondary microcontroller for basic motor/encoder interaction processing would be needed either way, as it has to be real-time processing. The display, on the other hand, could be connected to the RPI, the display is small enough to have little to none lag. Neither face recognition itself nor the decision-making have to happen on the CM, they could be delegated to the hub, but even transferring the images over wifi is heavy enough to consider having a secondary MCU solely dedicated to the haptic features.

scottbez1, 2022-10-03:
Cleaning up older issues. For reasons discussed (including https://github.com/scottbez1/smartknob/issues/64#issuecomment-1115502060), I don't think it will make sense to use to a full Linux system in place of the microcontroller, though we may want to change to a different microcontroller at some point.

Closed 2022-10-03.

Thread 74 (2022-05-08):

Debugging features : motor is not moving ...

shirogeek, 2022-05-08:
Hi there,

I finished assembly of everything and almost everything seemed to work on first boot (kind of an achievement knowing my track record).
This got me wondering if there is already or will be implemented debugging features which would allow you to single out faulty or unresponsive components. The assembly took me quite some time maybe because of my experience but such a feature would help accelerate debugging i would say.
Now specifically, in my case, the motor is unresponsive i feel no feedback at all. I am using an alternative : https://a.aliexpress.com/_mqVGhfy. It's a 12V rated brushless DC but from uni memory you can drive a motor irrelevant of voltage as long as current is enough to bypass cogging when static. I also have two others I haven't tried :
https://a.aliexpress.com/_mLbmAUa and
https://a.aliexpress.com/_mrdkyyE. Any advice on how I got about debugging this ? Are these motors even compatible to begin with ? Could I be guided into one or two lines of code I can add in the main.cpp to just make the motors rotate right or lzft at constant velocity (sanity check that the TMC chip works well) ?

Thanks a lot !

shirogeek, 2022-05-14:
I went ahead and did more tests today as I have again free time. I learned going through the issues that you can launch a calibration (motor specific) procedure by pressing Y at boot (thought it was for pressure sensing initially) and I can confirm something's wrong :

`Sensor measures positive for positive motor rotation: NO, Direction=CCW
HX711 reading: 576402
millilux: 43970.40
Going to measure 20 electrical revolutions...
Going to electrical zero...
pause...
HX711 reading: 579336
millilux: 43632.00
Measuring...
HX711 reading: 577822
millilux: 43732.80
HX711 reading: 576790
millilux: 43632.00
HX711 reading: 577252
millilux: 43732.80
HX711 reading: 577066
millilux: 43156.80
HX711 reading: 576430
millilux: 43336.80
Electrical angle / mechanical angle (i.e. pole pairs) = -263404.19
Pole pairs set to -263404
HX711 reading: 578487
millilux: 42508.80
HX711 reading: 578432
millilux: 42076.80
1.11, 80.30, 79.19

RESULTS:
  zero electric angle: 6.09
  direction: CCW
  pole pairs: -263404
`

This is the result of the calibration. I monitored the total current going to the system and it never changes. I assume therefore that there is a problem with my electronics ?
Next debugging steps I will look at U V W signals with my oscilloscope but just to clarify things, if I run the calibration the motor is expected to rotate correct ?

shirogeek, 2022-05-14:
Edit : I just realized a post already exists for this : https://github.com/scottbez1/smartknob/issues/36.
Sorry for duplicate... I will only reopen after steps in above issue are replicated.

shirogeek, 2022-05-14:
I managed to make it work...

Basically I debugged the signals and observed I wasn't getting any output at U V W or got only at V and W and nothing at U basically weird shaenenigans. My problem was that I was using low temp paste when I soldered the entire board. Being a very small package, low temp solder tends to not "draw" the chips to their proper alignment. I switched to regular temp solder paste and got it working on the first try. It is indeed a tricky chip to solder as scott mentioned.

Now I move on to investigating several motors and the possibility to use an HDD motor as drive (apparently has the lowest cogging possible). I will report my progress...

Closed 2022-05-14.

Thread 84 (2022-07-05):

Possibility of an even smaller size?

mardab, 2022-07-05:
I just saw [LILYGO T-QT V1.1](aliexpress.com/item/1005004405292321.html) which not just uses same-ish driving components (ESP32-S3 with GC9107 SPI display driver), but also has 0.85-inch 128×128 IPS LCD, which could make as a basis for smaller smart knob, one that fits where original cannot (as I have such case myself). I understand that this is not a round display, and if one at this scale cannot be found, I propose installing SK9822 LEDs in space to the sides of the display and cover them with white plastic diffuser ring, having to skip some corner pixels (or have them augment LEDs output), this way there can be even more space saved by skipping LED ring on the base. Aside from sorting that out, I am stumbled on the same problem the regular-sized knob, which is BLDC motor, and after a total of a week spent searching for some myself, my only hope is that [we might as well build our own motors](https://hackaday.io/project/39494-pcb-motor) and this smaller knob seems much easier to test this on.

5H4D0W-X, 2022-07-31:
A printed / pcb motor without a ferrite core will also completely eliminate the cogging problem that plagues most other motors

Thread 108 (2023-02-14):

Strain PADs still needed?

Tropaion, 2023-02-14:
Hello,
love this project, I soldered three PCBs of the old version where the strain gauges are still used and they are hell to solder.
Yesterday I saw they were replaced with resistors so I decided to make new PCBs and also decided to reduce the difficulty of soldering a bit. There is still much unused space on the platine so I decided to switch to bigger footprints and redraw the traces a bit (some are not that nice in my opinion).

It would be nice if there is a way to replace the motor controller with a bigger one but it looks like this is a pretty exotic one in terms of control (others I found use mostly SPI and I currently don't have time to dabble with the code).

Now, I'm not sure, but I think the strain pads aren't needed anymore and I can remove them, right?

Current progress:
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

Tropaion, 2023-02-22:
@scottbez1 If someone is interested, I improved the layout about, changed many footprints to bigger one to make soldering easier and added an optional connector (untested) for the display pcb to make disassembly easier.

[view_base.zip](https://github.com/scottbez1/smartknob/files/10808590/view_base.zip)

Closed 2023-02-22.

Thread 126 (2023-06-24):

Calibration problem

gregory353a, 2023-06-24:
During calibration motor won't start rotate without little push. It often fails whole calibration.

`Starting calibration, please DO NOT TOUCH MOTOR until complete!
LOG: HX711 reading: 1073822
LOG: millilux: 741.60
LOG: HX711 reading: 1074068
LOG: millilux: 741.60
LOG: HX711 reading: 1074621
LOG: Changing config to 0 -- Unbounded
No detents
LOG: Changing config to 1 -- Bounded 0-10
No detents
LOG: Changing config to 2 -- Multi-rev
No detents
LOG: Changing config to 3 -- On/off
Strong detent
LOG: millilux: 734.40
LOG: HX711 reading: 1077951
LOG: millilux: 734.40
LOG:
LOG: Sensor measures positive for positive motor rotation:
LOG: YES, Direction=CW
LOG: HX711 reading: 1075398
LOG: millilux: 734.40
LOG:   (start was 9.7, end was 11.5)
LOG: Going to measure 20 electrical revolutions...
LOG: Going to electrical zero...
LOG: HX711 reading: 1075476
LOG: pause...
LOG: millilux: 734.40
LOG: HX711 reading: 1075424
LOG: Measuring...
LOG: millilux: 734.40
LOG: HX711 reading: 1075550
LOG: millilux: 741.60
LOG: HX711 reading: 1075442
LOG: millilux: 734.40
LOG: HX711 reading: 1075107
LOG: millilux: 2124.00
LOG: HX711 reading: 1059738
LOG: millilux: 1116.00
LOG: HX711 reading: 146598
STATE: -1 [-6, 6]  (detent strength: 1.00, width: 60 deg, endstop strength: 1.00)
LOG: Electrical angle / mechanical angle (i.e. pole pairs) = -5675.98
LOG: ERROR! Unexpected calculated pole pairs: -5675.98
LOG: applying position change
LOG: adjusting detent center
LOG: Got new config
LOG: applying position change
LOG: adjusting detent center
LOG: Got new config
LOG: applying position change`

gregory353a, 2023-06-24:
```
Starting calibration, please DO NOT TOUCH MOTOR until complete!
LOG: millilux: 403.20
LOG: HX711 reading: 1075288
LOG: millilux: 583.20
LOG: HX711 reading: 1075457
LOG: millilux: 576.00
LOG: HX711 reading: 1075472
LOG: millilux: 583.20
LOG: HX711 reading: 1076203
LOG:
LOG: ERROR! Unexpected sensor change: start=10.56 end=10.56
```

jseyvecou, 2023-07-04:
Having the exact same issue, did you find any fix by any chance?

badaaim, 2023-07-14:
I am trying different motors to the one used in the project and I get similar weird values for pole pairs. Not sure if yours is the same case but at least for me if I switch back to the motor used in the project then I get more normal values like 7 for pole pairs.

gregory353a, 2023-07-16:
> Having the exact same issue, did you find any fix by any chance? I tried replacing some components like the MT6701-CT with a new one, but the issue persists. The motor I use is the one from SparkFun linked in the other thread

Unfortunately I didn't find problem yet. I will investigate, but I need some free time for that ;)

Jirik-Cermak, 2024-10-02:
> I am trying different motors to the one used in the project and I get similar weird values for pole pairs. Not sure if yours is the same case but at least for me if I switch back to the motor used in the project then I get more normal values like 7 for pole pairs.

Hello, I have the same issue. I see also 7 poles. What is a problem for me is, in two quadrants is encoder response to rotation higher and in two quadrant is the response less than reality.

I a good idea solve this by interpolation table? Do You have better idea?

Thank You
Jiri

xKraig, 2024-10-10:
> I have the same issue. The first calibration ran fine, but ever since I am getting either the "Unexpected sensor change" or "Unexpected calculated pole pairs" error.

To follow up on this, I fixed it by replacing the motor.

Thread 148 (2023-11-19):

Many improvements (battery, accelerometer, touch, MIDI, etc.)

DerSpatz, 2023-11-19:
First of all, I want to say that I really like the concept of the SmartKnob. That's why I decided to look into it more thoroughly and see where I can maybe add some improvements, some of which where also asked for here in the Github Issues. I am always trying to get the most out of a design, some might call it "feature creep".

# General Changes

First, I decided to go with a 4-layer PCB, where both inner layers are consecutive ground planes (plus some 5V fill on one layer). The top and bottom layers are signal, with a 3.3V fill. This improves signal integrity and EMI, and also makes routing (with good grounding) easier when space is limited, while the price is not that much higher than a 2-layer PCB.

Next, I moved the ESP32 to the bottom layer. This way, the ESP32 can be moved closer to the center of the PCB, as it does not collide with the outer ring of the top shell there. Now there's also enough space for an ESP32 in the WROOM form factor, so I went for the ESP32-S3, as it is faster, and has native USB, which might be useful if we want to use the SmartKnob as HID input device. My redesign is also ready to be used with a ESP32-S3-WROOM-2, which offers even faster flash and PSRAM. You just need to close one solder jumper for the WROOM-2. You can also use the "U" variant of the WROOM with an external antenna, which is also part of the PCB set.
I consider the WROOM module hand solderable, if you add a small plated slot to solder the center ground pads (used only for heatsinking). I also made sure that all parts on the back of the PCB are easy to hand solder, as are most of the top parts (min size 0603, enough distance between parts), except those darn small packages with bottom pads...

Then I cut down the corners of the PCB. You can still use a shell that has the shape of the original smart knob, but you can now also mount the SmartKnob in a round shell with 89mm or 84mm (U variant) diameter. The extra space can also be used for batteries (more on that later).
I also changed the PCB color to green, with a white silk screen ring where you can see it. The reason for this is simple: white 4-layer PCBs are much more expensive at JLCPCB, compared to green 4-layer.

Next, I made some mechanical changes: I moved the mounting holes on the PCB, as they where in a spot that was very tight, and I could not fit the necessary traces there otherwise. We also need a bit more space behind the PCB to accomodate some higher parts, but making the overall design 3-5mm higher should be enough. Please note that, while I considered and checked the feasibility of the mechanical changes, I did not do a mechanical redesign, yet (I'm not that good at 3D modeling).

At last, I added a PTC fuse for safety and TVS diodes to protect the USB and I2C lines. I also switched some parts:
The LDO voltage regulator was replaced with a DC-DC converter ([Texas Instruments TLV62569](https://www.ti.com/lit/ds/symlink/tlv62569.pdf)) for better efficiency.
The SK6812-SIDE-A LEDs where replaced with [WS2812-4020](https://www.peace-corp.co.jp/data/WS2812B-4020_V1.2_EN.pdf) LEDs. They are cheaper, have a built in capacitor (less work), and work with signal voltages down to 2.7V, so a level shifter is not needed anymore. _By the way, you can also power the first LED through a diode, the voltage drop works like a level shifter._
The light sensor was replaced with an THT analog version (looks like a LED). This allows for a wider variety in placement and parts choice. You could also mount the sensor through an opening in the top shell. The exact part number depends on your requirements in size (3mm or 5mm) and color (transparent or dark).

In the end, when all routing is done, I will also check where I can add some low height (max 6mm) bulk capacitors to the bottom side of the board for both power rails.

# New features:

Now that we have more space on the PCB and inside the case, we can start adding features...

## Accelerometer

The [ST LIS3DH](https://www.st.com/resource/en/datasheet/lis3dh.pdf) is a three axis accelerometer with interrupt output and ADC inputs. One ADC is used to read out the brightness sensor, the other ADC is used to read out the battery voltage.
With a built-in accelerometer (and USB support), turning the SmartKnob into a 3D mouse is much easier. My idea was to place the SmartKnob in a round case (hence the size reduction of the PCB) with a spherical bottom, which is then placed in a square baseplate with a mechanical design that allows movement of the SmartKnob while also keeping it centered. All necessary cables could be routed through a hole in the bottom.

## Battery Power

For battery power, I have designed an extra PCB around the [IP5306-I2C](http://www.injoinic.com/wwwroot/uploads/files/20200221/0405f23c247a34d3990ae100c8b20a27.pdf), which is an [I2C controlled](https://sharvielectronics.com/wp-content/uploads/2021/07/IP5306-I2C-registers.pdf) version of the IP5306. It charges a 3.7V lithium battery with 2.4A, while also delivering 5V/2.1A as a single chip solution. The power PCB is connected to the main PCB with two 5p 1.25mm cables (Molex PicoBlade). One is for power (5V, BAT, GND), and the other one transmits USB and I2C, so you can mount the power PCB into the bottom shell of the 3D SmartKnob and still use USB, without having a visible USB cable connected to the movable part of the 3D SmartKnob.

Please note that the batteries should not be too small, as they need to handle the charge and discharge current properly. Anything above 2000mAh should be enough. For the non-3D SmartKnob, you could add a flat (4-5mm) LiPo battery behind the main PCB. For the 3D SmartKnob, you could place up to 8 801350 LiPo batteries around the edge of the base unit.

On the main PCB the power input both from direct USB and the power PCB is controlled by a P-MOSFET. The gate from the PMOS can be controlled by the MCU (to keep it powered on), by a power button (as backup solution, for programming) or, most likely by the

## Touch Sensor

The [TTP233H-HA6](https://datasheet.lcsc.com/lcsc/2109061130_Tontek-Design-Tech-TTP233H-BA6_C2890349.pdf) is a single touch sensor. It is powered directly from the battery, but it has a very low standby current of 3µA, which should allow for a long standby time (The standby current of the IP5306 is 50µA). The input pin of the sensor is connected to one of the screw holes for the motor (I assume the motor is made of metal). This way the whole motor acts as an electrode and should be sensitive enough to detect if a hand is closing in on the SmartKnob, even though the distances are rather large. The MCU can also read out the output of the touch sensor, even though I assume this might be unreliable when the board is powered up, due to stray electric fields. But it should at least work when powered off. As a last measure, there's a solder jumper that adds a 100pF X7R 1206 capacitor in series to the much smaller sensing capacitor. The 1206 capacitor is placed on the bendy part of the PCB (just like the strain resistors), so a press on the SmartKnob should cause a change in capacitance in the 1206 capacitor, triggering the touch sensor.

**_The only question is: How long is the boot time? If it is too long, touch activation might not be a good user experience..._**

## Buttons

Besides the power button, I also added four additional switches around the edges of the PCB for user functions. These switches are side activated, so the button design on the top shell must have some kind of hinge and lever thingy that toggles the switches. This allows for much more freedom regarding the placement of the buttons. There are also some additional LEDs so the buttons can be illuminated if the lever/plunger of the switch is printed in a semi transparent material, with a cutout in the button shell showing the illuminated symbol.
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
Truetech000, 2023-11-20:
Yes, just yes! +1 from me.

feurer98, 2023-11-21:
i have no version built yet.  but I would join in here.  so +1

radu-boboc, 2023-11-21:
yes, it is awesome, please refine it further.

ChristianEmeis, 2023-11-25:
This looks really good, I would love to try this design when its finished 👍🏻

TKaluza, 2023-11-26:
Maybe adding zigbee would be nice, see [esp-docs ](https://docs.espressif.com/projects/esp-zigbee-sdk/en/latest/esp32/introduction.html)

DerSpatz, 2023-11-26:
@TKaluza The MIDI board is connected via UART, so using a ESP32-H2-WROOM module instead of the MIDI board should be possible, if you want ZigBee.

Design is mostly done, but I am still waiting for a word from @scottbez1 ...

florianL21, 2023-12-01:
I am just about to order all the parts but the esp32 is a major concern for me especially because of the missing support for native USB.
I would be happy to build and test this version of the electronics instead.
As for the required mechanical changes, I should be able to make the needed adjustments myself and am happy to contribute them once tested and working

DerSpatz, 2023-12-02:
@florianL21 Sounds good, let's get in contact!

Ich schicke dir nächste Woche mal ne Nachricht, bin übers Wochenende unterwegs...

radu-boboc, 2023-12-08:
All the improvements  you talked about, are they in a branch?
I would like to try them

DerSpatz, 2023-12-13:
Not yet, sorry. This is not ready for full release yet...

DerSpatz, 2023-12-13:
@florianL21 Ich sehe gerade, dass ich auf GitHub keine DMs senden kann. Kannst du mir eine EMail senden an: bastian bei mohi.ng (jo, nigerianische Domain, aber kein Scam ;-) )

radu-boboc, 2023-12-14:
I am curious if you ever considered a raspberry pi zero 2w.
From what I understood, and correct me if I am wrong, at this moment the project doesn't have WiFi so it can't be integrated with anything useful.
I am not gonna use it via usb, so In order to have more hardware resources we need a raspberry pi chip or something with more resources.

DerSpatz, 2023-12-14:
A Pi Zero 2W (or any Raspberry Pi) is not a good use case for this. Raspberry Pi runs a real Linux OS which, compared to a MCU, means:
- longer boot times
- higher power draw
- worse real time capabilities (needed for sensing and PWM controlling the dial)
- not enough pins
- way to much compute power

The ESP32 does have Wifi (and Bluetooth), and the ESP32-S3 even can be used as an USB HID device (which the Pi can't). After all, this is just a very sophisticated input device, so it should not need much computing power, that can be done by the system that takes the inputs.

radu-boboc, 2023-12-15:
Agreed with what you said, but can we use it to control stuff arround house? Oe use it to control stuff in windows/linux?
Can it send commands via WiFi (not usb) to target devices?

nicolabortignon, 2023-12-22:
@DerSpatz since you mentioned, have you got in your revision the knob to be recognized as a USB (C) HID device ?

kawashimaken, 2025-01-11:
@DerSpatz  Amazing! Do you have a GitHub Repo for this?

adamNewell, 2025-08-04:
Hi @DerSpatz, even in an unfinished state, it would be awesome if you could publish what you have so far. I'm super interested in finishing your version out!

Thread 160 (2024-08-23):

upload firmware - task failed

pippo93, 2024-08-23:
Hi all,
I was trying to follow these instructions (https://paper.dropbox.com/doc/SmartKnob-firmware-and-software-VUb9nq7btuhnHw5KlgJIH) to configure the new arrived SmartKnob Dev Kit 0.1 from SeedLabs.
Unfortunately, the process fail with this error:
`A fatal error occurred: This chip is ESP32-S3(beta3) not ESP32. Wrong --chip argument?`

Any suggestions?

frank-f, 2024-08-24:
Try using a lower baudrate. I've had to lower it to 460800 as well.

pippo93, 2024-09-03:
> Try using a lower baudrate. I've had to lower it to 460800 as well.

Tried to lower both “monitor_speed” and “upload_speed” in platformio.ini file as suggested but nothing changes.

frank-f, 2024-09-03:
Maybe double check all solder connections? Did you solder the components by hand or with stencil and reflow/hotplate? Try another CH340, if you have a spare?

pippo93, 2024-09-03:
> Maybe double check all solder connections? Did you solder the components by hand or with stencil and reflow/hotplate? Try another CH340, if you have a spare? Also, if you change the `monitor_speed` setting, make sure to also update `build_flags` accordingly, otherwise you're not going to see anything useful once you got the firmware to upload.

I boughy the assembled kit by SeedLabs. Today after one more try uploading the standard firmware as requested in the guide, the device definitely shut off (led and screen) and is no more recognized from the pc. I’ve asked to SeedLabs what I have to do because the device has now less then 15 minutes of life…

pippo93, 2024-09-07:
Faulty cable, sorry

Closed 2024-09-07.

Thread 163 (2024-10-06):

Can't flash firmware after manual boot mode

Oliver1948, 2024-10-06:
My base board has been completely soldered (minus the screen. I have tried many times to flash the firmware from vscode but it is not working. It says the following: Verbose mode can be enabled via `-v, --verbose` option
CONFIGURATION: https://docs.platformio.org/page/boards/espressif32/esp32doit-devkit-v1.html
PLATFORM: Espressif 32 (3.4.0) > DOIT ESP32 DEVKIT V1
HARDWARE: ESP32 240MHz, 320KB RAM, 4MB Flash
DEBUG: Current (esp-prog) External (esp-prog, iot-bus-jtag, jlink, minimodule, olimex-arm-usb-ocd, olimex-arm-usb-ocd-h, olimex-arm-usb-tiny-h, olimex-jtag-tiny, tumpa)
PACKAGES:
 - framework-arduinoespressif32 @ 3.10006.210326 (1.0.6)
 - tool-esptoolpy @ 1.30100.210531 (3.1.0)
 - tool-mkspiffs @ 2.230.0 (2.30)
 - toolchain-xtensa32 @ 2.50200.97 (5.2.0)
LDF: Library Dependency Finder -> https://bit.ly/configure-pio-ldf
LDF Modes: Finder ~ chain, Compatibility ~ soft
[nanopb] Installing Protocol Buffers dependencies
Requirement already satisfied: protobuf>=3.19.1 in c:\users\oaruf\.platformio\penv\lib\site-packages (5.28.2)
[nanopb] No generation needed.
Found 40 compatible libraries
Scanning dependencies...
Dependency Graph
|-- TLV493D-Magnetic-Sensor @ 1.0.3
|-- AceButton @ 1.9.1
|-- PacketSerial @ 1.4.0
|-- Nanopb @ 0.4.7
|-- Simple FOC @ 2.2.0
|-- TFT_eSPI @ 2.4.25
|-- FastLED @ 3.5.0
|-- HX711 @ 0.7.5
|-- Adafruit VEML7700 Library @ 1.1.1
|-- FFat @ 1.0
Building in release mode
Retrieving maximum program size .pio\build\view\firmware.elf
Checking size .pio\build\view\firmware.elf
Advanced Memory Usage is available via "PlatformIO Home > Project Inspect"
RAM:   [=         ]   6.6% (used 21716 bytes from 327680 bytes)
Flash: [====      ]  36.1% (used 473462 bytes from 1310720 bytes)
Configuring upload protocol...
AVAILABLE: esp-prog, espota, esptool, iot-bus-jtag, jlink, minimodule, olimex-arm-usb-ocd, olimex-arm-usb-ocd-h, olimex-arm-usb-tiny-h, olimex-jtag-tiny, tumpa
CURRENT: upload_protocol = esptool
Looking for upload port...
Auto-detected: COM7
Uploading .pio\build\view\firmware.bin
esptool.py v3.1
Serial port COM7
Connecting........_____....._____....._____....._____....._____....._____....._____

A fatal error occurred: Failed to connect to ESP32: Timed out waiting for packet header
*** [upload] Error 2
=============================================================== [FAILED] Took 29.85 seconds ===============================================================

Environment    Status    Duration
-------------  --------  ------------
view           FAILED    00:00:29.853
========================================================== 1 failed, 0 succeeded in 00:00:29.853 ==========================================================

 *  The terminal process "C:\Users\oaruf\.platformio\penv\Scripts\platformio.exe 'run', '--target', 'upload', '--target', 'monitor'" terminated with exit code: 1.
 *  Terminal will be reused by tasks, press any key to close it.

I saw a previous issue quite similar to mine, except for the fact that I have the transistors installed, and when I tried to manually enter the board into boot mode, nothing happened. In addition to all this, no lights turn on when I plug the board in, and the boot and en pins oscilate between 0 and 3.3v when attempting to connect. Below is a picture of my board for reference.
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

ChristianEmeis, 2024-10-07:
You need to use either U6 or U9, but not both. Maybe try to unsolder one of them and try again. If this does not help, try another USB-Cable, often upload errors are caused by faulty cables.

Oliver1948, 2024-10-07:
I have done both (new cable and removed U9), still nothing.

kawashimaken, 2024-12-14:
ch340c might be damaged, repace it with a new one, it may solve the problem.

kawashimaken, 2024-12-14:
> I have done both (new cable and removed U9), still nothing.
ch340c might be damaged, repace it with a new one, it may solve the problem.

Oliver1948, 2024-12-31:
Here's some more background info I should've put in my original issue. This board was ordered pcba from jlcpcb baring the microscopic motor chip and the main chip. Those are the two components I soldered on, and the board is not working. I am apprehensive to try and swap components that jlc installed cause I believe they tested everything before they sent it (doesn't mean I didn't fry something though 😂). Should I still swap ch340c?

Oliver1948, 2024-12-31:
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

Here's some more background info I should've put in my original issue. This board was ordered pcba from jlcpcb baring the microscopic motor chip and the main chip. Those are the two components I soldered on, and the board is not working. I am apprehensive to try and swap components that jlc installed cause I believe they tested everything before they sent it (doesn't mean I didn't fry something though 😂). Should I still swap ch340c, or should I focus on the things I installed?

Oliver1948, 2025-01-02:
Just figured out my issue and finally got it all working! I had to change the upload speed to 115200, and I had to change the board to pico32. This was all figured out after ChatGPT helped me finally get a terminal connected to the esp32 chip so I could pull info from it. So yeah, AI is taking over. Thanks to everyone for the help!

Closed 2025-01-02.

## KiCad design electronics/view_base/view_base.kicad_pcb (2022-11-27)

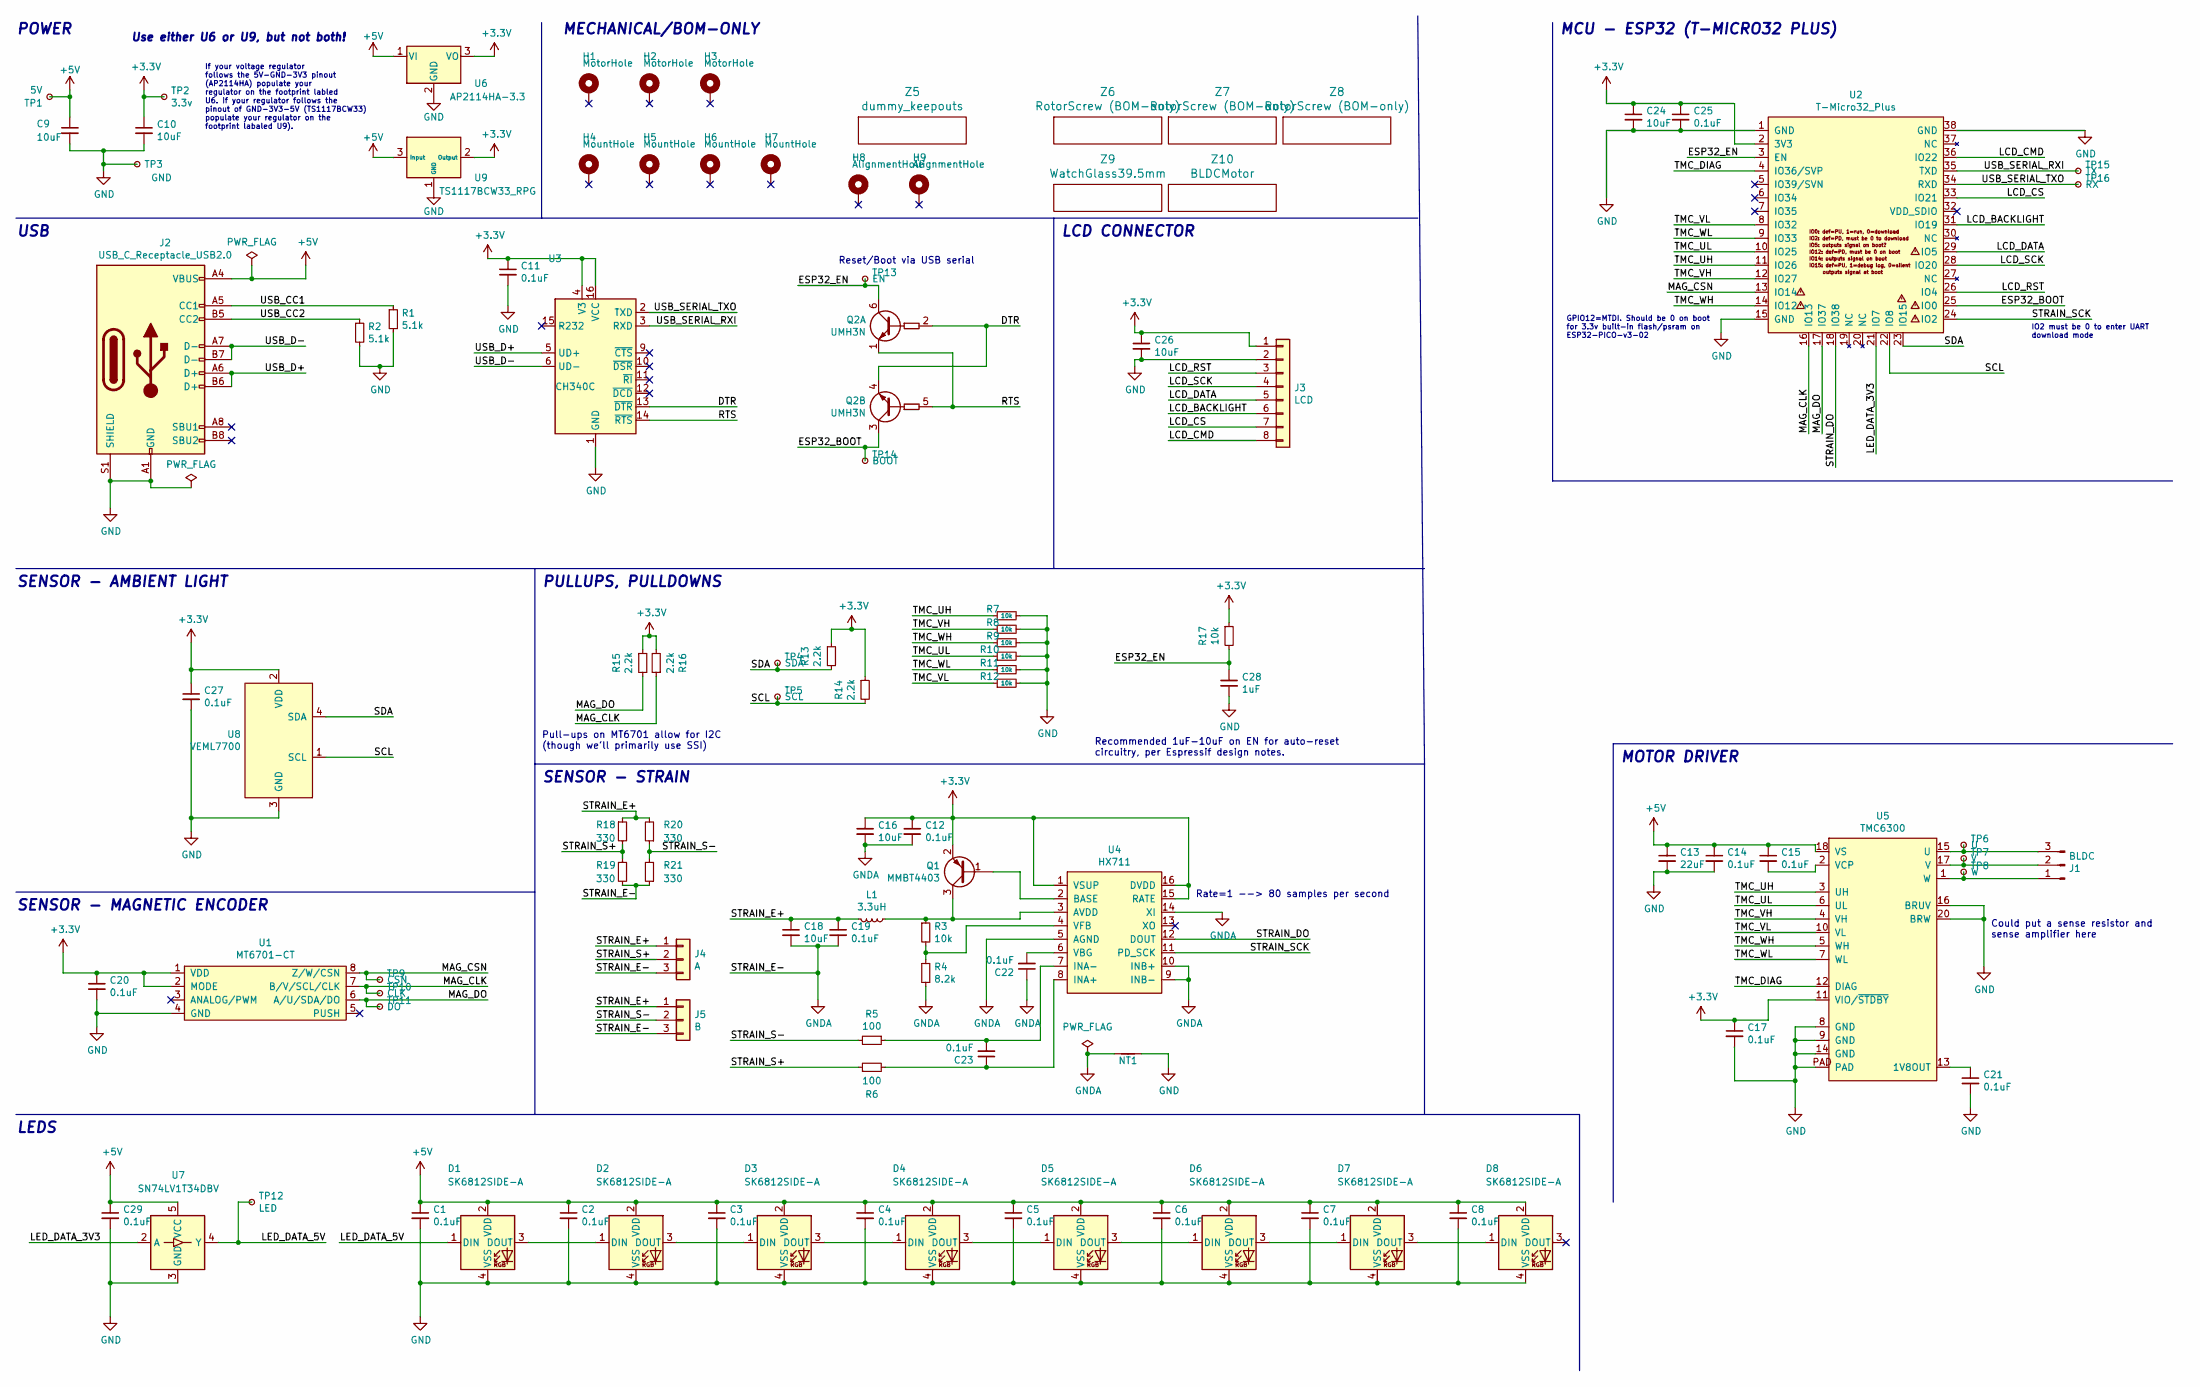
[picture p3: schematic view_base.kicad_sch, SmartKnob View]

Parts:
C1, C2, C3, C4, C5, C6, C7, C8, C11, C12, C14, C15, C17, C19, C20, C21, C22, C23, C25, C27, C29: 0.1uF; C_0603_1608Metric; LCSC C1591
C9, C10, C16, C18, C24, C26: 10uF; C_0805_2012Metric; LCSC C2922480
C13: 22uF; C_0805_2012Metric; LCSC C98190
C28: 1uF; C_0603_1608Metric; Mouser 187-CL10A105KA8NNNC
D1, D2, D3, D4, D5, D6, D7, D8: SK6812SIDE-A; SK6812-SIDE-A; Digikey 1528-4691-ND
H1, H2, H3: MotorHole; MountingHole_M1.6; LCSC C2931389
H4, H5, H6, H7: MountHole; MountingHole_2.2mm_M2_ISO7380_Pad_NonVirtual; LCSC C2911210 or C2911532 (screw), C2961595 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
H8, H9: AlignmentHole; MountingHole_2.2mm_M2_ISO7380_Pad_NonVirtual
J1: BLDC; 532610371; LCSC C293630
J2: USB_C_Receptacle_USB2.0; USB4510_NoPaste; LCSC C428463
J3: LCD; SolderPads_2mm_8
J4: A; SolderPads_2mm_3_STRAIN
J5: B; SolderPads_2mm_3_STRAIN
L1: 3.3uH; L_0805_2012Metric; LCSC C307744
NT1: NetTie_2; NetTie-2_SMD_Pad0.5mm
Q1: MMBT4403; SOT-23; LCSC C78864
Q2: UMH3N; SOT-363_SC-70-6; LCSC C62892
R1, R2: 5.1k; R_0603_1608Metric; LCSC C105580
R3, R7, R8, R9, R10, R11, R12, R17: 10k; R_0603_1608Metric; LCSC C98220
R4: 8.2k; R_0603_1608Metric; LCSC C114637
R5, R6: 100; R_0603_1608Metric; LCSC C319953
R13, R14, R15, R16: 2.2k; R_0603_1608Metric; LCSC C4190
R18, R19, R20, R21: 330; R_2512_6332Metric; LCSC C19866
TP1: 5V; TestPoint_Pad_D2.0mm_ValueSilk
TP2: 3.3v; TestPoint_Pad_D2.0mm_ValueSilk
TP3: GND; TestPoint_Pad_D2.0mm_ValueSilk
TP4: SDA; TestPoint_Pad_D2.0mm_ValueSilk
TP5: SCL; TestPoint_Pad_D2.0mm_ValueSilk
TP6: U; TestPoint_Pad_D2.0mm_ValueSilk
TP7: V; TestPoint_Pad_D2.0mm_ValueSilk
TP8: W; TestPoint_Pad_D2.0mm_ValueSilk
TP9: CSN; TestPoint_Pad_D2.0mm_ValueSilk
TP10: CLK; TestPoint_Pad_D2.0mm_ValueSilk
TP11: DO; TestPoint_Pad_D2.0mm_ValueSilk
TP12: LED; TestPoint_Pad_D2.0mm_ValueSilk
TP13: EN; TestPoint_Pad_D2.0mm_ValueSilk
TP14: BOOT; TestPoint_Pad_D2.0mm_ValueSilk
TP15: TX; TestPoint_Pad_D2.0mm_ValueSilk
TP16: RX; TestPoint_Pad_D2.0mm_ValueSilk
U1: MT6701-CT; SOIC-8_3.9x4.9mm_P1.27mm; LCSC C2856764, or C3003196
U2: T-Micro32_Plus; T-Micro32; Digikey N/A
U3: CH340C; SOIC-16_3.9x9.9mm_P1.27mm; LCSC C84681
U4: HX711; SOIC-16_3.9x9.9mm_P1.27mm; LCSC C43656
U5: TMC6300; QFN-20-1EP_3x3mm_P0.4mm_EP1.65x1.65mm_ThermalVias_LargerVia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; Digikey TMC6300-LA-T
U6: AP2114HA-3.3; SOT-223-3_TabPin2_InGndOut; LCSC C460314
U7: SN74LV1T34DBV; SOT-23-5; LCSC C100024
U8: VEML7700; VEML7700-TOP; Digikey VEML7700-TT
U9: TS1117BCW33_RPG; SOT-223-3_TabPin2_GndOutIn; LCSC C6186, C35879, or others
Z5: dummy_keepouts; ViewKeepouts3d
Z6, Z7, Z8: RotorScrew (BOM-only); bom_only_no_pin
Z9: WatchGlass39.5mm; bom_only_no_pin
Z10: BLDCMotor; bom_only_no_pin

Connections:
+3V3: C10.1, C11.1, C12.1, C16.1, C17.1, C20.1, C24.1, C25.1, C26.1, C27.1, J3.1, Q1.2 (E), R13.1, R14.1, R15.1, R16.2, R17.1, TP2.1, U1.1 (VDD), U1.2 (MODE), U2.2 (3V3), U3.4 (V3), U3.16 (VCC), U4.1 (VSUP), U4.15 (RATE), U4.16 (DVDD), U5.11 (VIO/~STDBY), U6.3 (VO), U8.2 (VDD), U9.2 (Output)
+5V: C1.1, C2.1, C3.1, C4.1, C5.1, C6.1, C7.1, C8.1, C9.1, C13.1, C14.1, C15.1, C29.1, D1.2 (VDD), D2.2 (VDD), D3.2 (VDD), D4.2 (VDD), D5.2 (VDD), D6.2 (VDD), D7.2 (VDD), D8.2 (VDD), J2.A4 (VBUS), J2.A9 (VBUS), J2.B4 (VBUS), J2.B9 (VBUS), TP1.1, U5.18 (VS), U6.1 (VI), U7.5 (VCC), U9.3 (Input)
/DTR: Q2.2 (B1), Q2.4 (E2), U3.13 (~DTR)
/ESP32_BOOT: Q2.3 (C2), TP14.1, U2.25 (IO0)
/ESP32_EN: C28.1, Q2.6 (C1), R17.2, TP13.1, U2.3 (EN)
/LCD_BACKLIGHT: J3.6, U2.31 (IO19)
/LCD_CMD: J3.8, U2.36 (IO22)
/LCD_CS: J3.7, U2.33 (IO21)
/LCD_DATA: J3.5, U2.29 (IO5)
/LCD_RST: J3.3, U2.26 (IO4)
/LCD_SCK: J3.4, U2.28 (IO20)
/LED_DATA_3V3: U2.21 (IO7), U7.2 (A)
/LED_DATA_5V: D1.1 (DIN), TP12.1, U7.4 (Y)
/MAG_CLK: R16.1, TP10.1, U1.7 (B/V/SCL/CLK), U2.16 (IO13)
/MAG_CSN: TP9.1, U1.8 (Z/W/CSN), U2.13 (IO14)
/MAG_DO: R15.2, TP11.1, U1.6 (A/U/SDA/DO), U2.17 (IO37)
/RTS: Q2.1 (E1), Q2.5 (B2), U3.14 (~RTS)
/SCL: R14.2, TP5.1, U2.22 (IO8), U8.1 (SCL)
/SDA: R13.2, TP4.1, U2.23 (IO15), U8.4 (SDA)
/STRAIN_DO: U2.18 (IO38), U4.12 (DOUT)
/STRAIN_E+: C18.1, C19.1, J4.1, J5.1, L1.2, R18.1, R20.2
/STRAIN_S+: J4.2, R6.1, R18.2, R19.1
/STRAIN_S-: J5.2, R5.2, R20.1, R21.2
/STRAIN_SCK: U2.24 (IO2), U4.11 (PD_SCK)
/TMC_DIAG: U2.4 (IO36/SVP), U5.12 (DIAG)
/TMC_UH: R7.1, U2.11 (IO26), U5.3 (UH)
/TMC_UL: R10.1, U2.10 (IO25), U5.6 (UL)
/TMC_VH: R8.1, U2.12 (IO27), U5.4 (VH)
/TMC_VL: R12.1, U2.8 (IO32), U5.10 (VL)
/TMC_WH: R9.1, U2.14 (IO12), U5.5 (WH)
/TMC_WL: R11.1, U2.9 (IO33), U5.7 (WL)
/USB_CC1: J2.A5 (CC1), R1.1
/USB_CC2: J2.B5 (CC2), R2.1
/USB_D+: J2.A6 (D+), J2.B6 (D+), U3.5 (UD+)
/USB_D-: J2.A7 (D-), J2.B7 (D-), U3.6 (UD-)
/USB_SERIAL_RXI: TP15.1, U2.35 (TXD), U3.3 (RXD)
/USB_SERIAL_TXO: TP16.1, U2.34 (RXD), U3.2 (TXD)
GND: C1.2, C2.2, C3.2, C4.2, C5.2, C6.2, C7.2, C8.2, C9.2, C10.2, C11.2, C13.2, C14.2, C17.2, C20.2, C21.2, C24.2, C25.2, C26.2, C27.2, C28.2, C29.2, D1.4 (VSS), D2.4 (VSS), D3.4 (VSS), D4.4 (VSS), D5.4 (VSS), D6.4 (VSS), D7.4 (VSS), D8.4 (VSS), J2.A1 (GND), J2.A12 (GND), J2.B1 (GND), J2.B12 (GND), J2.S1 (SHIELD), J3.2, NT1.2, R1.2, R2.2, R7.2, R8.2, R9.2, R10.2, R11.2, R12.2, TP3.1, U1.4 (GND), U2.1 (GND), U2.15 (GND), U2.38 (GND), U3.1 (GND), U5.8 (GND), U5.9 (GND), U5.14 (GND), U5.16 (BRUV), U5.20 (BRW), U5.PAD, U6.2 (GND), U7.3 (GND), U8.3 (GND), U9.1 (GND)
GNDA: C12.2, C16.2, C18.2, C19.2, C22.1, J4.3, J5.3, NT1.1, R4.2, R19.2, R21.1, U4.5 (AGND), U4.9 (INB-), U4.10 (INB+), U4.14 (XI)
unnamed: C15.2, U5.2 (VCP)
unnamed: C21.1, U5.13 (1V8OUT)
unnamed: C22.2, U4.6 (VBG)
unnamed: C23.1, R6.2, U4.8 (INA+)
unnamed: C23.2, R5.1, U4.7 (INA-)
unnamed: D1.3 (DOUT), D2.1 (DIN)
unnamed: D2.3 (DOUT), D3.1 (DIN)
unnamed: D3.3 (DOUT), D4.1 (DIN)
unnamed: D4.3 (DOUT), D5.1 (DIN)
unnamed: D5.3 (DOUT), D6.1 (DIN)
unnamed: D6.3 (DOUT), D7.1 (DIN)
unnamed: D7.3 (DOUT), D8.1 (DIN)
unnamed: J1.1, TP8.1, U5.1 (W)
unnamed: J1.2, TP7.1, U5.17 (V)
unnamed: J1.3, TP6.1, U5.15 (U)
unnamed: L1.1, Q1.3 (C), R3.1, U4.3 (AVDD)
unnamed: Q1.1 (B), U4.2 (BASE)
unnamed: R3.2, R4.1, U4.4 (VFB)

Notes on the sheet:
POWER
Could put a sense resistor and sense amplifier here
MCU - ESP32 (T-MICRO32 PLUS)
If your voltage regulator follows the 5V-GND-3V3 pinout (AP2114HA) populate your regulator on the footprint labled U6. If your regulator follows the pinout of GND-3V3-5V (TS1117BCW33) populate your regulator on the footprint labaled U9).
SENSOR - MAGNETIC ENCODER
MOTOR DRIVER
MECHANICAL/BOM-ONLY
IO2 must be 0 to enter UART download mode
GPIO12=MTDI. Should be 0 on boot for 3.3v built-in flash/psram on ESP32-PICO-v3-02
Pull-ups on MT6701 allow for I2C (though we'll primarily use SSI)
Use either U6 or U9, but not both!
Rate=1 --> 80 samples per second
SENSOR - AMBIENT LIGHT
Recommended 1uF-10uF on EN for auto-reset circuitry, per Espressif design notes.
USB
SENSOR - STRAIN
LEDS
PULLUPS, PULLDOWNS
LCD CONNECTOR
Reset/Boot via USB serial

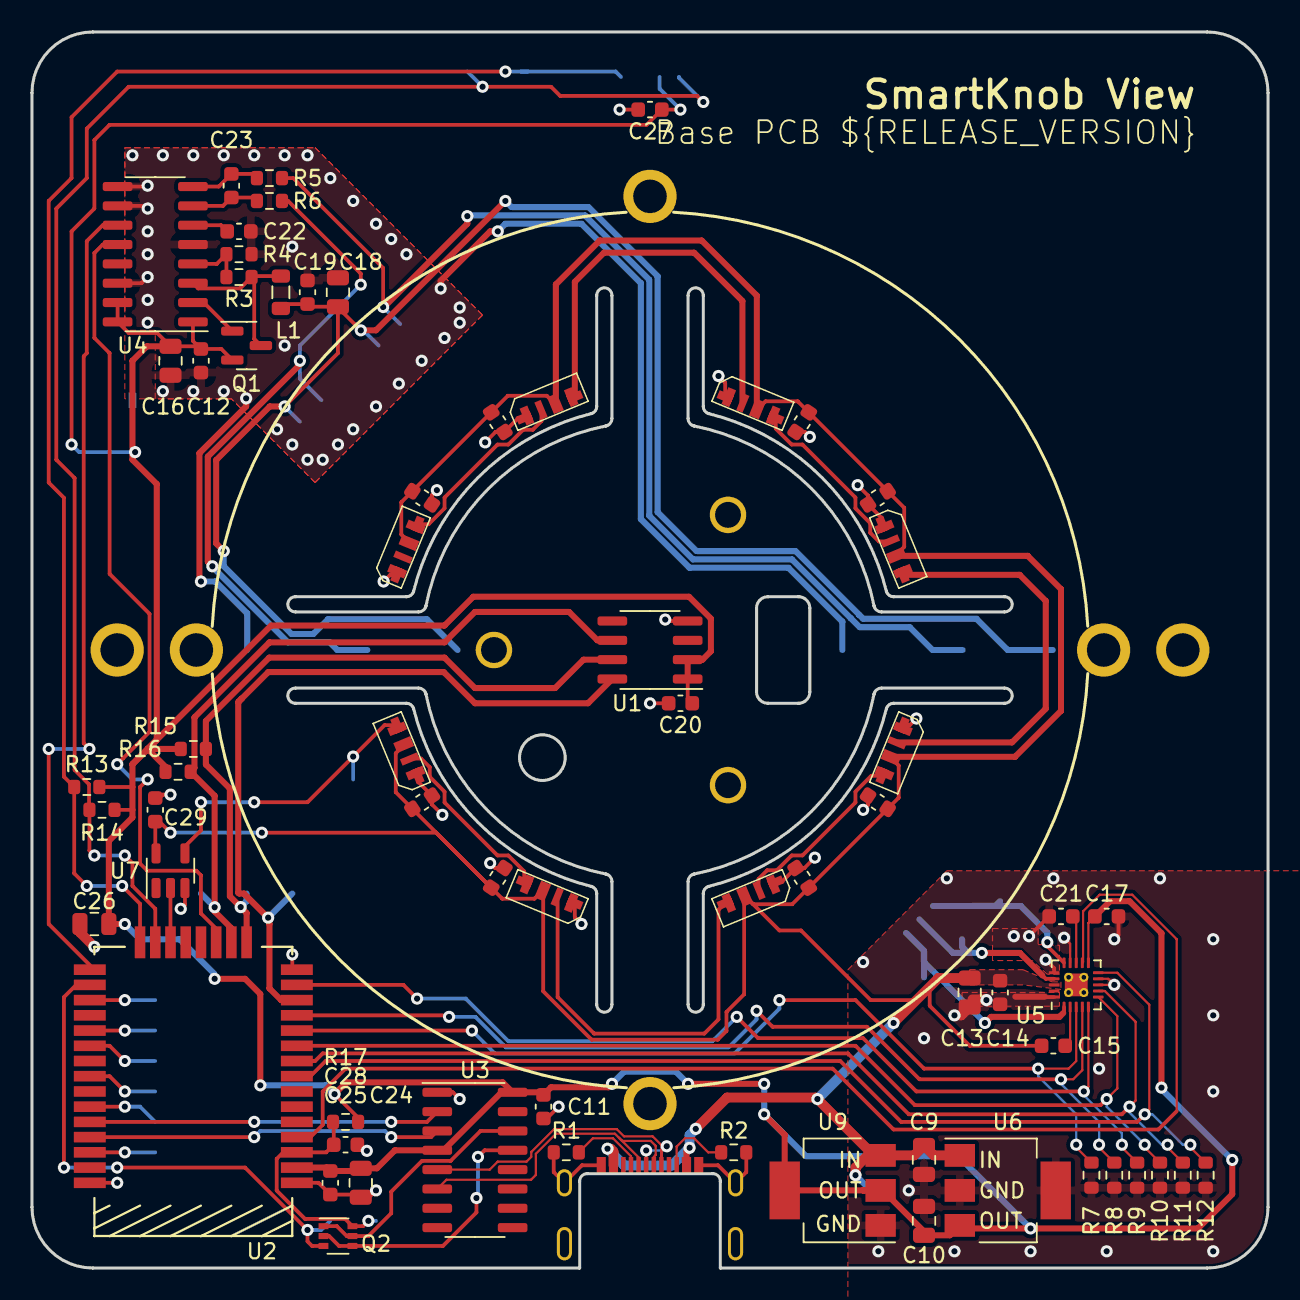
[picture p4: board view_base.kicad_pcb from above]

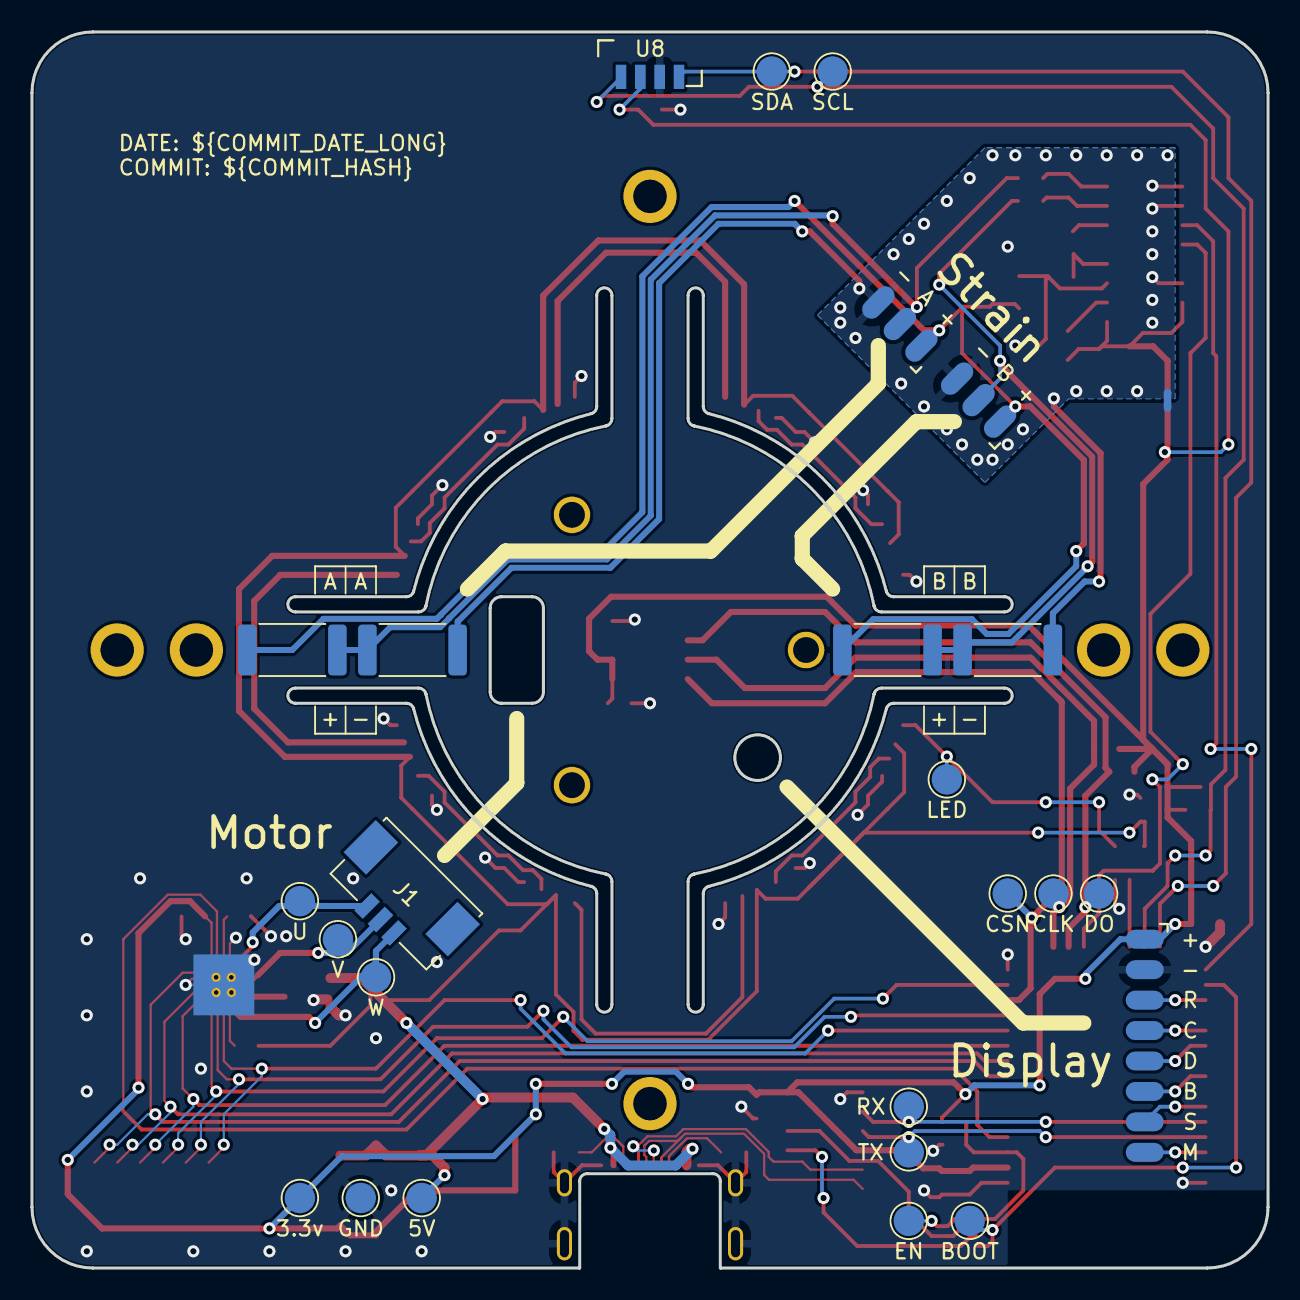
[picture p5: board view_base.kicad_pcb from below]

Board: 2 copper layers, 81.2 x 81.2 mm, 107 parts (26 on the bottom side), 57 nets.

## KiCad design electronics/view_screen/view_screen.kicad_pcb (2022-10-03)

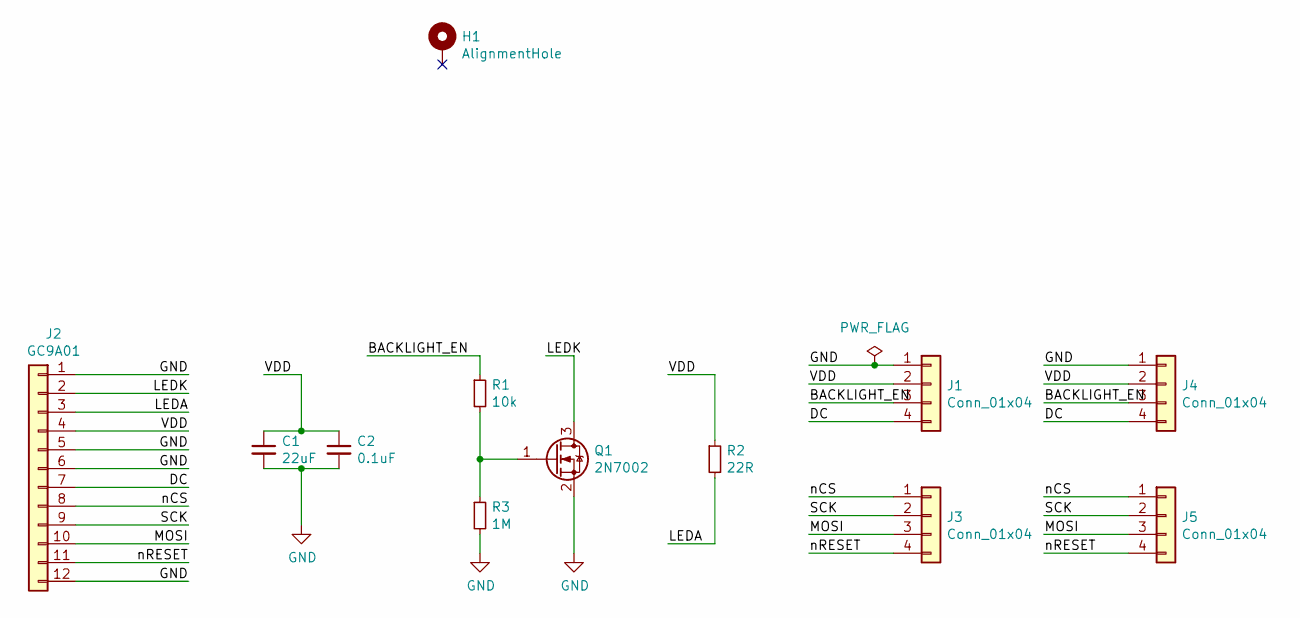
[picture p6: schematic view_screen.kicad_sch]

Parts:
C1: 22uF; C_0805_2012Metric; Digikey 1276-CL21A226MAYNNNECT-ND
C2: 0.1uF; C_0603_1608Metric; Digikey 1276-1935-1-ND
H1: AlignmentHole; AlignmentHole_1.6
J1, J3, J4, J5: Conn_01x04; SolderPads_2mm_4
J2: GC9A01; GC9A01Round1.28; Digikey N/A
Q1: 2N7002; SOT-23; Digikey 2N7002H6327XTSA2CT-ND
R1: 10k; R_0603_1608Metric; Digikey RMCF0603JT10K0CT-ND
R2: 22R; R_0603_1608Metric; Digikey RMCF0603JT22R0CT-ND
R3: 1M; R_0603_1608Metric; Digikey RMCF0603JT1M00CT-ND

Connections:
/BACKLIGHT_EN: J1.3, J4.3, R1.1
/DC: J1.4, J2.7, J4.4
/LEDA: J2.3, R2.2
/LEDK: J2.2, Q1.3 (D)
/MOSI: J2.10, J3.3, J5.3
/SCK: J2.9, J3.2, J5.2
/VDD: C1.1, C2.1, J1.2, J2.4, J4.2, R2.1
/nCS: J2.8, J3.1, J5.1
/nRESET: J2.11, J3.4, J5.4
GND: C1.2, C2.2, J1.1, J2.1, J2.5, J2.6, J2.12, J4.1, Q1.2 (S), R3.2
unnamed: Q1.1 (G), R1.2, R3.1

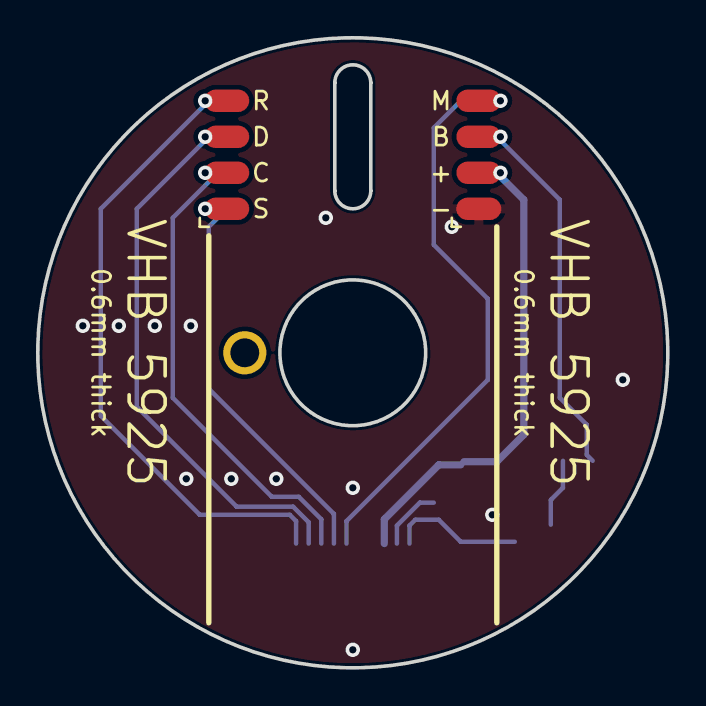
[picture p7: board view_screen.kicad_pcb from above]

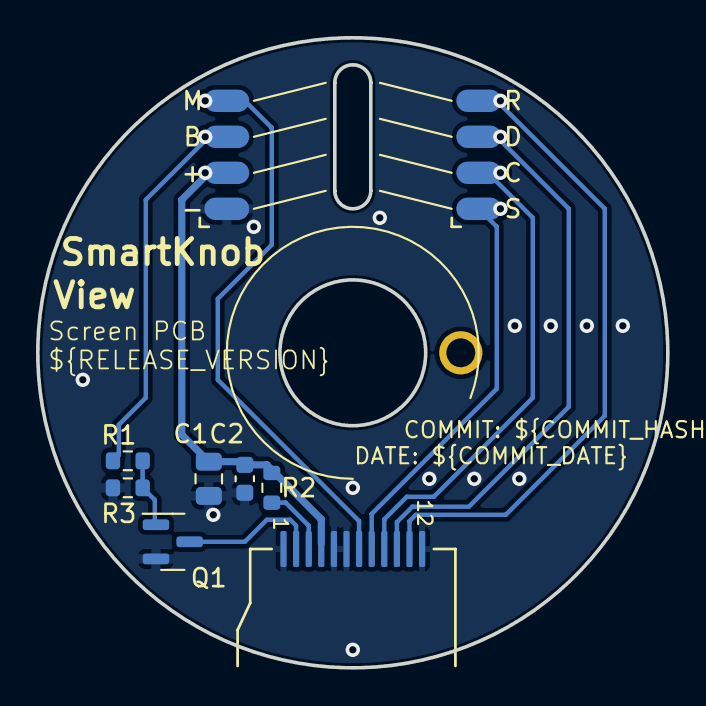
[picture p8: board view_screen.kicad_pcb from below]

Board: 2 copper layers, 35.0 x 35.0 mm, 12 parts (9 on the bottom side), 11 nets.

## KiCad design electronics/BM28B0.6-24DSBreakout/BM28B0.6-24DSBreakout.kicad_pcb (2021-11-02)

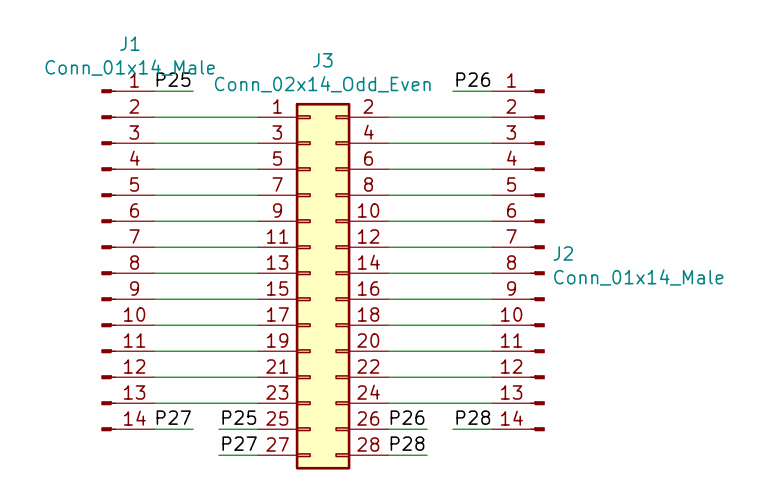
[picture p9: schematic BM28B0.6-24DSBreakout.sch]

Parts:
J1, J2: Conn_01x14_Male; PinHeader_1x14_P2.54mm_Vertical
J3: Conn_02x14_Odd_Even; BM28B0.6-24DS

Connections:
/P25: J1.1, J3.25
/P26: J2.1, J3.26
/P27: J1.14, J3.27
/P28: J2.14, J3.28
unnamed: J1.2, J3.1
unnamed: J1.3, J3.3
unnamed: J1.4, J3.5
unnamed: J1.5, J3.7
unnamed: J1.6, J3.9
unnamed: J1.7, J3.11
unnamed: J1.8, J3.13
unnamed: J1.9, J3.15
unnamed: J1.10, J3.17
unnamed: J1.11, J3.19
unnamed: J1.12, J3.21
unnamed: J1.13, J3.23
unnamed: J2.2, J3.2
unnamed: J2.3, J3.4
unnamed: J2.4, J3.6
unnamed: J2.5, J3.8
unnamed: J2.6, J3.10
unnamed: J2.7, J3.12
unnamed: J2.8, J3.14
unnamed: J2.9, J3.16
unnamed: J2.10, J3.18
unnamed: J2.11, J3.20
unnamed: J2.12, J3.22
unnamed: J2.13, J3.24

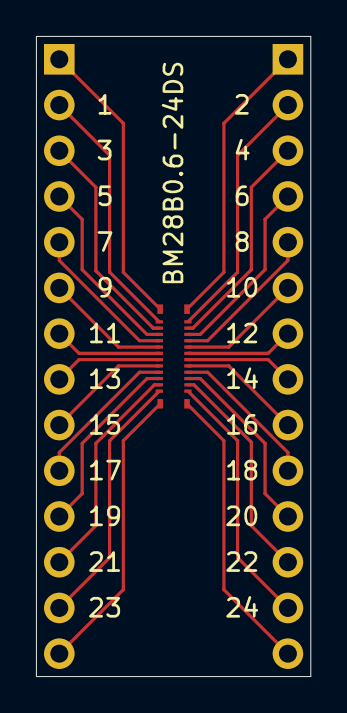
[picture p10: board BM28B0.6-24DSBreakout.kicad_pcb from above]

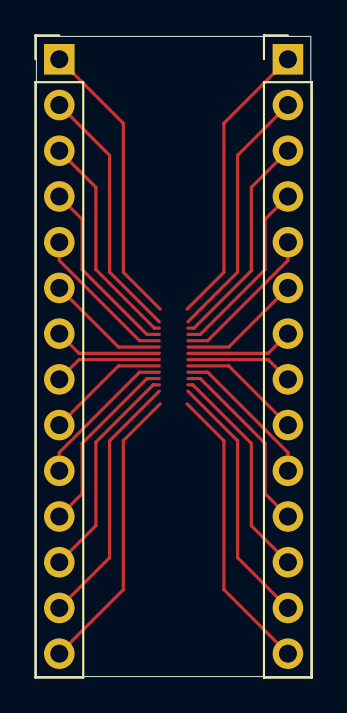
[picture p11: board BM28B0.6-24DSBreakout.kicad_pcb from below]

Board: 2 copper layers, 15.2 x 35.6 mm, 3 parts (2 on the bottom side), 28 nets.

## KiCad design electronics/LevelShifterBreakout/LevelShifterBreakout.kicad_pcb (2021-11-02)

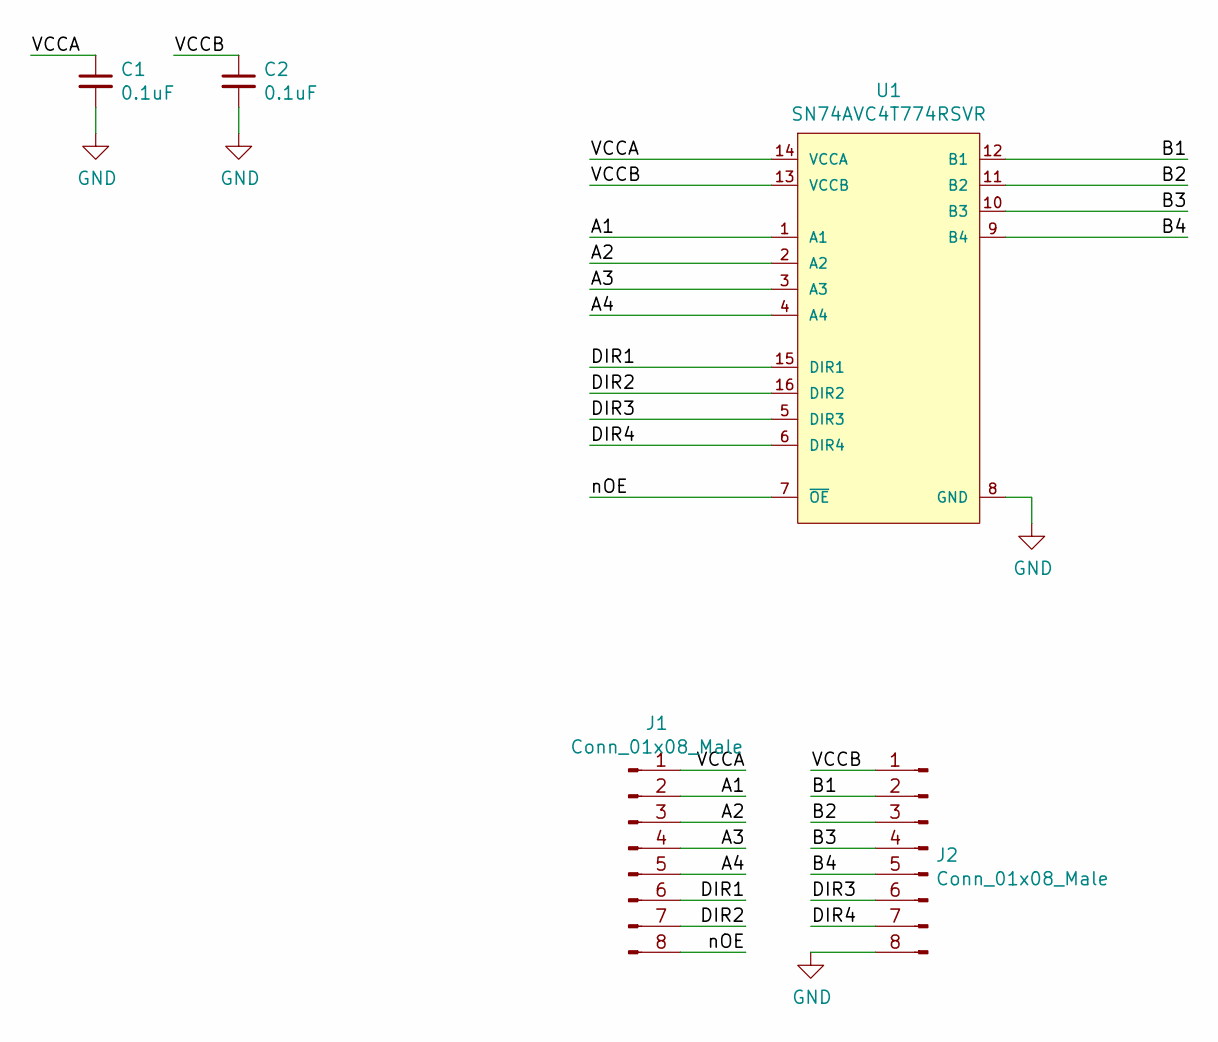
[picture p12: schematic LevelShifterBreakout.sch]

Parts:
C1, C2: 0.1uF; C_0805_2012Metric_Pad1.18x1.45mm_HandSolder
J1, J2: Conn_01x08_Male; PinHeader_1x08_P2.54mm_Vertical
U1: SN74AVC4T774RSVR; Texas_Instruments-RSV_R-PUQFN-N16-0-0-0; Voltage - VCCA 1.2V ~ 3.6V; Voltage - VCCB 1.2V ~ 3.6V; mouser part number 595-SN74AVC4T774RSVR; digikey description Voltage Level Translator Bidirectional 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

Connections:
/A1: J1.2, U1.1 (A1)
/A2: J1.3, U1.2 (A2)
/A3: J1.4, U1.3 (A3)
/A4: J1.5, U1.4 (A4)
/B1: J2.2, U1.12 (B1)
/B2: J2.3, U1.11 (B2)
/B3: J2.4, U1.10 (B3)
/B4: J2.5, U1.9 (B4)
/DIR1: J1.6, U1.15 (DIR1)
/DIR2: J1.7, U1.16 (DIR2)
/DIR3: J2.6, U1.5 (DIR3)
/DIR4: J2.7, U1.6 (DIR4)
/VCCA: C1.1, J1.1, U1.14 (VCCA)
/VCCB: C2.1, J2.1, U1.13 (VCCB)
/nOE: J1.8, U1.7 (~OE~)
GND: C1.2, C2.2, J2.8, U1.8 (GND)

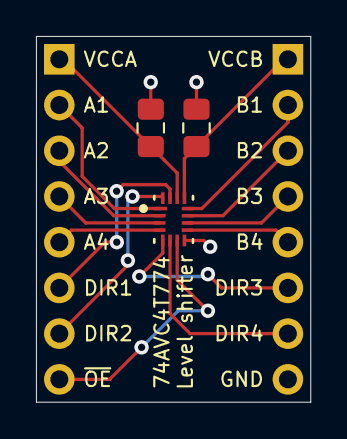
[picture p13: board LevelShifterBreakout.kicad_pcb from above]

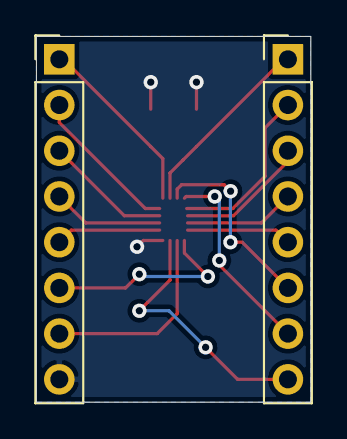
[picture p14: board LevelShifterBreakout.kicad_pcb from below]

Board: 2 copper layers, 15.2 x 20.3 mm, 5 parts (2 on the bottom side), 16 nets.

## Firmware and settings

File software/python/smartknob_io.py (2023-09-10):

if __name__ == '__main__':
    import sys
    sys.exit('This is a library file to be imported into your own python scripts. It doesn\'t do anything if run directly')


from cobs import cobs
from collections import (
    defaultdict,
)
from contextlib import contextmanager
from enum import Enum
import logging
import os
from queue import (
    Empty,
    Full,
    Queue,
)
from random import randint
import serial
import serial.tools.list_ports
import sys
from threading import (
    Thread,
    Lock,
)
import time
import zlib

software_root = os.path.dirname(os.path.abspath(__file__))
sys.path.append(os.path.join(software_root, 'proto_gen'))

from proto_gen import smartknob_pb2

SMARTKNOB_BAUD = 921600
PROTOBUF_PROTOCOL_VERSION = 1


class Smartknob(object):
    RETRY_TIMEOUT = 0.25

    def __init__(self, serial_instance):
        self._serial = serial_instance
        self._logger = logging.getLogger('smartknob')
        self._out_q = Queue()
        self._ack_q = Queue()
        self._next_nonce = randint(0, 255)
        self._run = True

        self._lock = Lock()
        self._message_handlers = defaultdict(list)

    def _read_loop(self):
        self._logger.debug('Read loop started')
        buffer = b''
        while True:
            buffer += self._serial.read_until(b'\0')
            if not self._run:
                return

            if not len(buffer):
                continue

            if not buffer.endswith(b'\0'):
                continue
            
            self._process_frame(buffer[:-1])
            buffer = b''

    def _process_frame(self, frame):
        try:
            decoded = cobs.decode(frame)
        except cobs.DecodeError:
            self._logger.debug(f'Failed decode ({len(frame)} bytes)')
            self._logger.debug(frame)
            return

        if len(decoded) < 4:
            return

        payload = decoded[:-4]
        expected_crc = zlib.crc32(payload) & 0xffffffff
        provided_crc = (decoded[-1] << 24) \
                        | (decoded[-2] << 16) \
                        | (decoded[-3] << 8) \
                        | decoded[-4]
        
        if expected_crc != provided_crc:
            self._logger.debug(f'Bad CRC. expected={hex(expected_crc)}, actual={hex(provided_crc)}')
            return

        message = smartknob_pb2.FromSmartKnob()
        message.ParseFromString(payload)
        self._logger.debug(message)
        if message.protocol_version != PROTOBUF_PROTOCOL_VERSION:
            self._logger.warn(f'Invalid protocol version. Expected {PROTOBUF_PROTOCOL_VERSION}, received {message.protocol_version}')

        payload_type = message.WhichOneof('payload')

        # If this is an ack, notify the write thread
        if payload_type == 'ack':
            nonce = message.ack.nonce
            self._ack_q.put(nonce)

        with self._lock:
            for handler in self._message_handlers[payload_type] + self._message_handlers[None]:
                try:
                    handler(getattr(message, payload_type))
                except:
                    self._logger.warning(f'Unhandled exception in message handler ({payload_type})', exc_info=True)
    
    def _write_loop(self):
        self._logger.debug('Write loop started')
        while True:
            data = self._out_q.get()
            # Check for shutdown
            if not self._run:
                self._logger.debug('Write loop exiting @ _out_q')
                return
            (nonce, encoded_message) = data

            next_retry = 0
            while True:
                if time.time() >= next_retry:
                    if next_retry > 0:
                        self._logger.debug('Retry write...')
                    self._serial.write(encoded_message)
                    self._serial.write(b'\0')
                    next_retry = time.time() + Smartknob.RETRY_TIMEOUT
                
                try:
                    latest_ack_nonce = self._ack_q.get(timeout=next_retry - time.time())
                except Empty:
                    latest_ack_nonce = None

                # Check for shutdown
                if not self._run:
                    self._logger.debug('Write loop exiting @ _ack_q')
                    return

                if latest_ack_nonce == nonce:
                    break
                else:
                    self._logger.debug(f'Got unexpected nonce: {latest_ack_nonce}')
    
    def _enqueue_message(self, message):
        nonce = self._next_nonce
        self._next_nonce += 1

        message.protocol_version = PROTOBUF_PROTOCOL_VERSION
        message.nonce = nonce

        payload = bytearray(message.SerializeToString())

        crc = zlib.crc32(payload) & 0xffffffff
        payload.append(crc & 0xff)
        payload.append((crc >> 8) & 0xff)
        payload.append((crc >> 16) & 0xff)
        payload.append((crc >> 24) & 0xff)

        encoded_message = cobs.encode(payload)

        self._out_q.put((nonce, encoded_message))

        approx_q_length = self._out_q.qsize()
        self._logger.debug(f'Out q length: {approx_q_length}')
        if approx_q_length > 10:
            self._logger.warning(f'Output queue length is high! ({approx_q_length}) Is the smartknob still connected and functional?')

    def set_config(self, config):
        message = smartknob_pb2.ToSmartknob()
        message.smartknob_config.CopyFrom(config)
        self._enqueue_message(message)

    def start(self):
        self.read_thread = Thread(target=self._read_loop)
        self.write_thread = Thread(target=self._write_loop)
        self.read_thread.start()
        self.write_thread.start()
    
    def shutdown(self):
        self._logger.info('Shutting down...')
        self._run = False
        self.read_thread.join()
        self._logger.debug('Read thread terminated')
        self._out_q.put(None)
        self._ack_q.put(None)
        self.write_thread.join()
        self._logger.debug('Write thread terminated')
    
    def add_handler(self, message_type, handler):
        with self._lock:
            self._message_handlers[message_type].append(handler)
        return lambda: self._remove_handler(message_type, handler)

    def _remove_handler(self, message_type, handler):
        with self._lock:
            self._message_handlers[message_type].remove(handler)

    def request_state(self):
        message = smartknob_pb2.ToSmartknob()
        message.request_state.SetInParent()
        self._enqueue_message(message)

    def hard_reset(self):
        self._serial.setRTS(True)
        self._serial.setDTR(False)
        time.sleep(0.2)
        self._serial.setDTR(True)
        time.sleep(0.2)


@contextmanager
def smartknob_context(serial_port, default_logging=True, wait_for_comms=True):
    with serial.Serial(serial_port, SMARTKNOB_BAUD, timeout=1.0) as ser:
        s = Smartknob(ser)
        s.start()

        if default_logging:
            s.add_handler('log', lambda msg: s._logger.info(f'From smartknob: {msg.msg}'))

        if wait_for_comms:
            s._logger.info('Connecting to smartknob...')
            q = Queue(1)
            def startup_handler(message):
                try:
                    q.put_nowait(None)
                except Full:
                    pass
            unregister = s.add_handler('smartknob_state', startup_handler)

            s.request_state()
            q.get()
            unregister()
            s._logger.info('Connected!')

        try:
            yield s
        finally:
            s.shutdown()


def ask_for_serial_port():
    """
    Helper function to ask which port to use via stdin
    """
    print('Available ports:')
    ports = sorted(
        filter(
            lambda p: p.description != 'n/a',
            serial.tools.list_ports.comports(),
        ),
        key=lambda p: p.device,
    )
    for i, port in enumerate(ports):
        print('[{: 2}] {} - {}'.format(i, port.device, port.description))
    print()
    value = input('Use which port? ')
    port_index = int(value)
    assert 0 <= port_index < len(ports)
    return ports[port_index].device

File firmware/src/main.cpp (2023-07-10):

#include <Arduino.h>

#include "configuration.h"
#include "display_task.h"
#include "interface_task.h"
#include "motor_task.h"

Configuration config;

#if SK_DISPLAY
static DisplayTask display_task(0);
static DisplayTask* display_task_p = &display_task;
#else
static DisplayTask* display_task_p = nullptr;
#endif
static MotorTask motor_task(1, config);


InterfaceTask interface_task(0, motor_task, display_task_p);

void setup() {
  #if SK_DISPLAY
  display_task.setLogger(&interface_task);
  display_task.begin();

  // Connect display to motor_task's knob state feed
  motor_task.addListener(display_task.getKnobStateQueue());
  #endif

  interface_task.begin();

  config.setLogger(&interface_task);
  config.loadFromDisk();

  interface_task.setConfiguration(&config);

  motor_task.setLogger(&interface_task);
  motor_task.begin();

  // Free up the Arduino loop task
  vTaskDelete(NULL);
}

void loop() {
  // char buf[50];
  // static uint32_t last_stack_debug;
  // if (millis() - last_stack_debug > 1000) {
  //   interface_task.log("Stack high water:");
  //   snprintf(buf, sizeof(buf), "  main: %d", uxTaskGetStackHighWaterMark(NULL));
  //   interface_task.log(buf);
  //   #if SK_DISPLAY
  //     snprintf(buf, sizeof(buf), "  display: %d", uxTaskGetStackHighWaterMark(display_task.getHandle()));
  //     interface_task.log(buf);
  //   #endif
  //   snprintf(buf, sizeof(buf), "  motor: %d", uxTaskGetStackHighWaterMark(motor_task.getHandle()));
  //   interface_task.log(buf);
  //   snprintf(buf, sizeof(buf), "  interface: %d", uxTaskGetStackHighWaterMark(interface_task.getHandle()));
  //   interface_task.log(buf);
  //   snprintf(buf, sizeof(buf), "Heap -- free: %d, largest: %d", heap_caps_get_free_size(MALLOC_CAP_8BIT), heap_caps_get_largest_free_block(MALLOC_CAP_8BIT));
  //   interface_task.log(buf);
  //   last_stack_debug = millis();
  // }
}

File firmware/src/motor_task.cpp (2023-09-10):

#include <SimpleFOC.h>

#include "motor_task.h"
#if SENSOR_MT6701
#include "mt6701_sensor.h"
#elif SENSOR_TLV
#include "tlv_sensor.h"
#elif SENSOR_MAQ430
#include "maq430_sensor.h"
#endif

#include "motors/motor_config.h"
#include "util.h"

static const float DEAD_ZONE_DETENT_PERCENT = 0.2;
static const float DEAD_ZONE_RAD = 1 * _PI / 180;

static const float IDLE_VELOCITY_EWMA_ALPHA = 0.001;
static const float IDLE_VELOCITY_RAD_PER_SEC = 0.05;
static const uint32_t IDLE_CORRECTION_DELAY_MILLIS = 500;
static const float IDLE_CORRECTION_MAX_ANGLE_RAD = 5 * PI / 180;
static const float IDLE_CORRECTION_RATE_ALPHA = 0.0005;


MotorTask::MotorTask(const uint8_t task_core, Configuration& configuration) : Task("Motor", 4000, 1, task_core), configuration_(configuration) {
    queue_ = xQueueCreate(5, sizeof(Command));
    assert(queue_ != NULL);
}

MotorTask::~MotorTask() {}


#if SENSOR_TLV
    TlvSensor encoder = TlvSensor();
#elif SENSOR_MT6701
    MT6701Sensor encoder = MT6701Sensor();
#elif SENSOR_MAQ430
    MagneticSensorSPI encoder = MagneticSensorSPI(MAQ430_SPI, PIN_MAQ_SS);
#endif

void MotorTask::run() {

    driver.voltage_power_supply = 5;
    driver.init();

    #if SENSOR_TLV
    encoder.init(&Wire, false);
    #elif SENSOR_MT6701
    encoder.init();
    #elif SENSOR_MAQ430
    SPIClass* spi = new SPIClass(HSPI);
    spi->begin(PIN_MAQ_SCK, PIN_MAQ_MISO, PIN_MAQ_MOSI, PIN_MAQ_SS);
    encoder.init(spi);
    #endif

    motor.linkDriver(&driver);

    motor.controller = MotionControlType::torque;
    motor.voltage_limit = FOC_VOLTAGE_LIMIT;
    motor.velocity_limit = 10000;
    motor.linkSensor(&encoder);

    // Not actually using the velocity loop built into SimpleFOC; but I'm using those PID variables
    // to run PID for torque (and SimpleFOC studio supports updating them easily over serial for tuning)
    motor.PID_velocity.P = FOC_PID_P;
    motor.PID_velocity.I = FOC_PID_I;
    motor.PID_velocity.D = FOC_PID_D;
    motor.PID_velocity.output_ramp = FOC_PID_OUTPUT_RAMP;
    motor.PID_velocity.limit = FOC_PID_LIMIT;

    #ifdef FOC_LPF
    motor.LPF_angle.Tf = FOC_LPF;
    #endif

    motor.init();

    encoder.update();
    delay(10);

    PB_PersistentConfiguration c = configuration_.get();
    motor.pole_pairs = c.motor.calibrated ? c.motor.pole_pairs : 7;
    motor.initFOC(c.motor.zero_electrical_offset, c.motor.direction_cw ? Direction::CW : Direction::CCW);

    motor.monitor_downsample = 0; // disable monitor at first - optional

    // disableCore0WDT();

    float current_detent_center = motor.shaft_angle;
    PB_SmartKnobConfig config = {
        .position = 0,
        .sub_position_unit = 0,
        .position_nonce = 0,
        .min_position = 0,
        .max_position = 1,
        .position_width_radians = 60 * _PI / 180,
        .detent_strength_unit = 0,
    };
    int32_t current_position = 0;
    float latest_sub_position_unit = 0;

    float idle_check_velocity_ewma = 0;
    uint32_t last_idle_start = 0;
    uint32_t last_publish = 0;

    while (1) {
        motor.loopFOC();

        // Check queue for pending requests from other tasks
        Command command;
        if (xQueueReceive(queue_, &command, 0) == pdTRUE) {
            switch (command.command_type) {
                case CommandType::CALIBRATE:
                    calibrate();
                    break;
                case CommandType::CONFIG: {
                    // Check new config for validity
                    PB_SmartKnobConfig& new_config = command.data.config;
                    if (new_config.detent_strength_unit < 0) {
                        log("Ignoring invalid config: detent_strength_unit cannot be negative");
                        break;
                    }
                    if (new_config.endstop_strength_unit < 0) {
                        log("Ignoring invalid config: endstop_strength_unit cannot be negative");
                        break;
                    }
                    if (new_config.snap_point < 0.5) {
                        log("Ignoring invalid config: snap_point must be >= 0.5 for stability");
                        break;
                    }
                    if (new_config.detent_positions_count > COUNT_OF(new_config.detent_positions)) {
                        log("Ignoring invalid config: detent_positions_count is too large");
                        break;
                    }
                    if (new_config.snap_point_bias < 0) {
                        log("Ignoring invalid config: snap_point_bias cannot be negative or there is risk of instability");
                        break;
                    }

                    // Change haptic input mode
                    bool position_updated = false;
                    if (new_config.position != config.position
                            || new_config.sub_position_unit != config.sub_position_unit
                            || new_config.position_nonce != config.position_nonce) {
                        log("applying position change");
                        current_position = new_config.position;
                        position_updated = true;
                    }

                    if (new_config.min_position <= new_config.max_position) {
                        // Only check bounds if min/max indicate bounds are active (min >= max)
                        if (current_position < new_config.min_position) {
                            current_position = new_config.min_position;
                            log("adjusting position to min");
                        } else if (current_position > new_config.max_position) {
                            current_position = new_config.max_position;
                            log("adjusting position to max");
                        }
                    }

                    if (position_updated || new_config.position_width_radians != config.position_width_radians) {
                        log("adjusting detent center");
                        float new_sub_position = position_updated ? new_config.sub_position_unit : latest_sub_position_unit;
                        #if SK_INVERT_ROTATION
                            float shaft_angle = -motor.shaft_angle;
                        #else
                            float shaft_angle = motor.shaft_angle;
                        #endif
                        current_detent_center = shaft_angle + new_sub_position * new_config.position_width_radians;
                    }
                    config = new_config;
                    log("Got new config");
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

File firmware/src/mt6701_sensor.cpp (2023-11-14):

#include "mt6701_sensor.h"
#include "driver/spi_master.h"

static const float ALPHA = 0.4;


static uint8_t tableCRC6[64] = {
 0x00, 0x03, 0x06, 0x05, 0x0C, 0x0F, 0x0A, 0x09,
 0x18, 0x1B, 0x1E, 0x1D, 0x14, 0x17, 0x12, 0x11,
 0x30, 0x33, 0x36, 0x35, 0x3C, 0x3F, 0x3A, 0x39,
 0x28, 0x2B, 0x2E, 0x2D, 0x24, 0x27, 0x22, 0x21,
 0x23, 0x20, 0x25, 0x26, 0x2F, 0x2C, 0x29, 0x2A,
 0x3B, 0x38, 0x3D, 0x3E, 0x37, 0x34, 0x31, 0x32,
 0x13, 0x10, 0x15, 0x16, 0x1F, 0x1C, 0x19, 0x1A,
 0x0B, 0x08, 0x0D, 0x0E, 0x07, 0x04, 0x01, 0x02
};

/*32-bit input data, right alignment, Calculation over 18 bits (mult. of 6) */
static uint8_t CRC6_43_18bit (uint32_t w_InputData)
{
 uint8_t b_Index = 0;
 uint8_t b_CRC = 0;

 b_Index = (uint8_t )(((uint32_t)w_InputData >> 12u) & 0x0000003Fu);

 b_CRC = (uint8_t )(((uint32_t)w_InputData >> 6u) & 0x0000003Fu);
 b_Index = b_CRC ^ tableCRC6[b_Index];

 b_CRC = (uint8_t )((uint32_t)w_InputData & 0x0000003Fu);
 b_Index = b_CRC ^ tableCRC6[b_Index];

 b_CRC = tableCRC6[b_Index];

 return b_CRC;
} 

#if SENSOR_MT6701

MT6701Sensor::MT6701Sensor() {}

void MT6701Sensor::init() {

    pinMode(PIN_MT_CSN, OUTPUT);
    digitalWrite(PIN_MT_CSN, HIGH);

  spi_bus_config_t tx_bus_config = {
      .mosi_io_num = -1,
      .miso_io_num = PIN_MT_DATA,
      .sclk_io_num = PIN_MT_CLOCK,
      .quadwp_io_num = -1,
      .quadhd_io_num = -1,
      .max_transfer_sz = 1000,
  };
  
  #ifdef CONFIG_IDF_TARGET_ESP32S3
    esp_err_t ret = spi_bus_initialize(SPI3_HOST, &tx_bus_config, SPI_DMA_CH_AUTO);
  #else
    esp_err_t ret = spi_bus_initialize(HSPI_HOST, &tx_bus_config, 1);
  #endif
  
  ESP_ERROR_CHECK(ret);

  spi_device_interface_config_t tx_device_config = {
      .command_bits=0,
      .address_bits=0,
      .dummy_bits=0,
      .mode=1,
      .duty_cycle_pos=0,
      .cs_ena_pretrans=4,
      .cs_ena_posttrans=0,
      .clock_speed_hz=4000000,
      .input_delay_ns=0,
      .spics_io_num=PIN_MT_CSN,
      .flags = 0,
      .queue_size=1,
      .pre_cb=NULL,
      .post_cb=NULL,
  };
  #ifdef CONFIG_IDF_TARGET_ESP32S3
    ret=spi_bus_add_device(SPI3_HOST, &tx_device_config, &spi_device_);
  #else
    ret=spi_bus_add_device(HSPI_HOST, &tx_device_config, &spi_device_);
  #endif
  
  ESP_ERROR_CHECK(ret);


  spi_transaction_.flags = SPI_TRANS_USE_RXDATA;
  spi_transaction_.length = 24;
  spi_transaction_.rxlength = 24;
  spi_transaction_.tx_buffer = NULL;
  spi_transaction_.rx_buffer = NULL;
}

float MT6701Sensor::getSensorAngle() {
    uint32_t now = micros();
    if (now - last_update_ > 100) {
      
      esp_err_t ret=spi_device_polling_transmit(spi_device_, &spi_transaction_);
      assert(ret==ESP_OK);

      uint32_t spi_32 = (spi_transaction_.rx_data[0] << 16) | (spi_transaction_.rx_data[1] << 8) | spi_transaction_.rx_data[2];
      uint32_t angle_spi = spi_32 >> 10;

      uint8_t field_status = (spi_32 >> 6) & 0x3;
      uint8_t push_status = (spi_32 >> 8) & 0x1;
      uint8_t loss_status = (spi_32 >> 9) & 0x1;

      uint8_t received_crc = spi_32 & 0x3F;
      uint8_t calculated_crc = CRC6_43_18bit(spi_32 >> 6);
      
      if (received_crc == calculated_crc) {
        float new_angle = (float)angle_spi * 2 * PI / 16384;
        float new_x = cosf(new_angle);
        float new_y = sinf(new_angle);
        x_ = new_x * ALPHA + x_ * (1-ALPHA);
        y_ = new_y * ALPHA + y_ * (1-ALPHA);
      } else {
        error_ = {
          .error = true,
          .received_crc = received_crc,
          .calculated_crc = calculated_crc,
        };
      }

      last_update_ = now;
    }
    float rad = -atan2f(y_, x_);
    if (rad < 0) {
        rad += 2*PI;
    }
    return rad;
}

MT6701Error MT6701Sensor::getAndClearError() {
  MT6701Error out = error_;
  error_ = {};
  return out;
}

#endif

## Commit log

2021-10-22 initial checkin
    [shaftMount.scad]
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2021-11-02 Check in initial electronics projects
    [BM28B0.6-24DSBreakout.kicad_pcb, BM28B0.6-24DSBreakout.sch, LevelShifterBreakout.kicad_pcb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]
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2022-01-16 Reduce noise on coarse detents
    [display_task.cpp, interface_task.cpp, motor_task.cpp]
2022-02-09 Checkpoint View PCB
    [view.kicad_pcb, view.sch]
2022-02-10 View: Update pin assignments on ESP32 to avoid potential boot issues
    [view.sch]
2022-02-11 View: PCB checkpoint
    [view.kicad_pcb, view.sch]
2022-02-11 View: finished initial routing
    [view.kicad_pcb, view.sch]
2022-02-11 View: Small pcb tweaks
    [view.kicad_pcb]
2022-02-12 View: Add initial screen pcb
    [view.kicad_pcb, view.sch, view_screen.kicad_pcb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]
2022-02-13 View: screen pcb nearly done
    [view_screen.kicad_pcb]
2022-02-13 View: rename base pcb to view_base
    [view_base.kicad_pcb, view_base.sch]
2022-02-13 View: Label LCD pads
    [view_base.kicad_pcb, view_screen.kicad_pcb]
2022-02-13 View: improve silk
    [view_base.kicad_pcb, view_base.sch]
2022-02-14 Add EN pullup, capacitor, test points
    [view_base.kicad_pcb, view_base.sch]
2022-02-15 KiBot electronics automation (#1)
    Basic KiBot artifact generation - schematic, bom, and pbc renders
    [view_base.kicad_pcb]
2022-02-15 Fab automation (#2)
    - Use KiKit for fab automation
    - Add splitflap scripts for exporting pcb pdfs, and switch to splitflap script for 3d rendering (for consistency with fab automation)
    - Added support in 3d rendering scripts for soldermask & silkscreen colors, option to skip virtual components
    - Added silkscreen to base and screen pcbs for commit and date info
    [view_base.kicad_pcb, view_screen.kicad_pcb]
2022-02-15 View screen pcb: move solderpads to bottom to avoid shorting on metal LCD shield
    [view_screen.kicad_pcb]
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2022-02-15 Remove paste from USB-C pads
    USB-C connector will be soldered separately from main top reflow, since it hangs below the board.
    [view_base.kicad_pcb, view_base.sch]
2022-02-15 Clean up schematic
    [view_base.sch]
2022-02-16 View base: Fix GND fill under TMC6300
    [view_base.kicad_pcb]
2022-02-16 Change View Base to v0.2
    [view_base.kicad_pcb]
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2022-03-11 Firmware updates - sensors, calibration, View support, etc (#9)
    - Modify TLV493d library to expose frame counter in order to check for lockup, and implement auto-reset in tlv_sensor in case of lockup
    - Implement MT6701 SimpleFOC sensor
    - Make display optional
    - Add optional LED, strain, ALS support
    - Connect ALS to LED and display brightness
    - Hardcoded strain gauge thresholds and haptic feedback
    [display_task.cpp, interface_task.cpp, interface_task.h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]
2022-03-11 Fix HX711 analog supply, fix 3.3v regulator
    Fixes #8
    Fixes #3
    [view_base.kicad_pcb, view_base.sch]
2022-03-13 Add a bunch of part numbers to BOM
    [smartknob.kicad_pcb, smartknob.sch, view_base.kicad_pcb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]
2022-03-13 Remove "service loop" silkscreen marks from screen pcb
    Service loops weren't really feasible/helpful, so don't recommend them via the silkscreen. Fixes #10
    Also added testpoints (or could be solder points) for all signals on the top side of the screen PCB. Fixes #11
    [view_screen.kicad_pcb, view_screen.sch]
2022-03-14 Generate merged BOM (#15)
    Also add more bom-only items to the schematic
    [view_base.kicad_pcb, view_base.sch]
2022-03-15 Add alignment holes, update board outline - shorter slots
    Fixes #7
    [view_base.kicad_pcb, view_base.sch]
2022-03-15 Add testpoints for RX and TX
    Updates #14
    [view_base.kicad_pcb, view_base.sch]
2022-03-15 Update README.md
    Add notes about artifacts being auto-generated and untested. Also add link to potential other motor listing. Updates #16
2022-03-15 Fix LCD footprint lib path and hide LCD 3d model by default in kicad 3d rendering
    [view_screen.kicad_pcb]
2022-03-16 Move C10 slightly so that paste/stencil matches v0.2
    [view_base.kicad_pcb]
2022-03-24 Update readme - motors are no longer available :(
2022-03-31 Update README.md
    Some updates and clarifications on the motor situation and current project status
2022-04-07 Cleanup old pio envs, fix some compilation issues with compile flags
    Removed some legacy platformio envs that are not actively being maintained. But also fixed some bugs with different build flags that caused compilation issues.
    Fixes #49
    [display_task.cpp, mt6701_sensor.cpp]
2022-04-07 Increase motor task stack
    Avoid accidental stack overflows from small stack.
    Updates #37
    Updates #50
    [motor_task.cpp]
2022-05-28 Fix compilation error if SK_ALS=0 but PIN_SDA and PIN_SCL are set
    [interface_task.cpp]
2022-09-27 Motor is available from SparkFun
    [view_base.sch]
2022-10-03 Migrate to KiCad 6 (#96)
    - Updated view_base and view_screen KiCad projects to v6 files
    - Updated footprints to v6 versions
    - Fixed all DRC errors and most warnings
    - Updated CI
    - Run on Ubuntu 22.04 runner
    - Updated KiBot and KiKit versions
    - Use KiBot for 3d rendering now instead of custom scripts
    - Switched to using KiCad text variables for replacement rather than raw text find&replace
    - Misc design updates
    - Exposed bottom-side thermal pad underneath TMC6300 to make it easier to possibly hand-solder
    - Separated GND and GNDA nets, replaced connection with a net-tie, and updated corresponding copper fills around HX711
    [view_base.kicad_pcb, view_base.kicad_sch, view_base.sch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]
2022-10-11 Adding second footprint for 3V3 voltage regulator (#98)
    The voltage regulator that was originally used isn't available at the moment. To provide more options, a second footprint was added to the PCB for an alternative regulator that has a different pinout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
    Also, adjusted .gitignore for Mac files and KiCad auto-generated backups.
    [view_base.kicad_pcb, view_base.kicad_sch]
2022-10-11 Add BOM entries and note for new LDO
    Also clean up PCB:
    - Make LDOs mirror each other on board
    - Custom footprints with silkscreen "in" "gnd" "out" labels
    [view_base.kicad_pcb, view_base.kicad_sch]
2022-10-11 Add alternative MT6701 LCSC/JLC part number
    [view_base.kicad_sch]
2022-10-11 Fix placeholder replacement for kikit gerber exports
2022-10-23 Protobuf serial protocol (#101)
    - Firmware
    - Refactor all code to use a log interface rather than `Serial` directly
    - Moved platformio.ini to root, so you can load the entire repo in VS Code and still use platformio
    - Reduced graphic buffer bit depth to 8 bits (short on RAM :( )
    - Implemented threadsafe log interface in interface_task (using a queue for posting log message)
    - Created serial protocol interface and 2 implementations - plaintext (default) and protobuf (selected by sending a NULL byte)
    - Protobuf protocol is roughly the same architecture as Splitflap's:
    - PacketSerial (cobs) framing with NULL delimiters
    - CRC32 checksums for packets
    - nanopb gene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
    [display_task.cpp, interface_task.cpp, interface_task.h]
2022-10-27 Quick lowercase hack to help Windows users (#103)
    Windows upper cases the vendor and product id, so the filter will fail.
    So LOWERCASE ALL THE THINGS!
2022-11-13 LCSC part numbers and notes for M1.6/M2 hardware
    [view_base.kicad_sch]
2022-11-27 Use 2512 SMD resistors in place of strain gauges (#104)
    As suggested in https://github.com/scottbez1/smartknob/issues/24#issuecomment-1073540944 and inspired by https://github.com/IvDm/Z-probe-on-smd-resistors-2512, this adds 4x 330 ohm 2512 SMD resistors to the back to act as strain gauges, rather than requiring discrete strain gauges to be glued and wired up.
    Also applies a few changes I accidentally had pending locally:
    - Custom footprints for the 2 3.3v LDO options to clarify the pinout options
    ![image](https://user-images.githubusercontent.com/414890/204078474-8327e8ed-78b5-4fe3-a91d-9c20fe54fcbc.png)
    - some BOM note updates
    Fixes #24
    Closes #33
    [view_base.kicad_pcb, view_base.kicad_sch]
2023-01-16 New detent configurations (magnetic and biased-to-center) and demo React app (#105)
    Breaking change to protobuf messages to support new detent configurations - adds more flexibility compared to existing config parameters (e.g. min/max position rather than just number of positions).
    New magnetic detent mode allows for config to specify up to 5 nearest detent positions (with smooth scrolling in between them); the intent is a higher-level controller (e.g. connected demo app, see b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
    ---
    React demo app implements a mock video editor timeline, with the ability to inter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
2023-02-04 Python software example (#106)
    Add protobuf/cobs/crc32 framework code and a really basic python example
2023-05-30 NanoFOC/ESP32-S3 support (#117)
    - New PlatformIO env (`nanofoc`) for the NanoFOC hardware
    - Huge thanks to @lgc00 for the initial NanoFOC configuration and prototyping!
    - Uses `HWCDC` rather than `UartStream` as the serial `Stream` interface (ESP32-S3 specific change)
    - Support for MAQ430 magnetic encoder sensor
    - Motor-specific PID tuning constants moved to separate header files
    ---------
2023-06-14 Use TFT_eSprite.drawNumber for the current position (#118)
    I would suggest using `drawNumber` instead of drawString to align each
    digit of the number to the same width and erase the jittering effect
    when the current position is changed.
    [display_task.cpp]
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2023-06-14 Updated config schema, improved demo (#121)
    - Breaking proto updates
    - added position nonce to config, and added ability to specify a
    sub_position via config as well => more flexibility to control position
    via config
    - added version as first field of serial protocol messages, so future
    breaking proto updates can easily be detected and ignored
    - Fixed up web-based demo of a mock video editor/timeline jog/playback
    controller
    - Fixed config/state flow so that mode changes correctly maintain
    playback position
    - Demo: https://www.youtube.com/watch?v=J9192DfZplk
    [interface_task.cpp, motor_task.cpp]
2023-06-15 SPIFFS persistent storage for motor calibration (#122)
    - New Configuration class for managing persistent configuration
    - New proto messages for serialized configuration, with flexibility for
    expansion
    - Load persistent configuration at startup, if available, use for
    default motor calibration
    - Save motor calibration to persistent configuration file
    [configuration.h]
2023-06-16 Add missing partition file and update GH actions to run nanofoc build
    [partitions-4MB-spiffs.csv]
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2023-06-17 Revert "SPIFFS persistent storage for motor calibration (#122)"
    Seems to be causing weird behavior/performance with the motor control loop, particularly noticeable with fine detents. Reverting for now until I have a chance to investigate further.
    This reverts commit 1d73af17cc24d0cd464f24ee4073363a7b0045f0.
    [configuration.h]
2023-06-19 Implement persistent configuration/calibration storage using FFAT (#124)
    Reintroduces persistent configuration from #122, but using FFAT instead
    of SPIFFS, since SPIFFS had bad performance impacts on the motor control
    loop.
    [configuration.h, partitions-4MB-fat.csv]
2023-07-10 Strain calibration
    [configuration.h]
2023-07-10 Fix GitHub Actions path filters w/ globs
2023-09-10 Demo improvements (#135)
    - LED hue config
    - press state reporting
    - custom display modes for timeline demo
2023-10-28 BOM - Replace discontinued C2922480 with C15850
    Fixes #139 - thanks @lorhof1 and @Wilgelmy
    [view_base.kicad_sch]
2023-11-14 Fine tuning for esp32s3 (#143)
    - exposed strain SCK and DO
    - use 12 bit PWM (instead of 16 bit) for screen brightness on s3
    - added option to use uart serial for s3
    - bump nanopb/Nanopb @ 0.4.7
    - fixed SPI bus alias and DMA channel for s3
    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
    [display_task.cpp, interface_task.cpp, interface_task.h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]

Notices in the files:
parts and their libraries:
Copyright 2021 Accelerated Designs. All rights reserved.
